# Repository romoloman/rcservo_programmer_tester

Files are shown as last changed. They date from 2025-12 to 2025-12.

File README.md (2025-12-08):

# RC Servo Programmer/Tester on Cheap Yellow Display*

A project to use a "Cheap Yellow Display" (based on ESP32) as Servo Programmer/Tester

## Project Description

This repository contains the code and instructions to turn a simple ESP32-based "Cheap Yellow Display" into a practical servo programmer and tester for RC Servo:
The tester work on any servo while at the moment the programmer works only on PTK Servos (other are planned to be supported). 
It allows you to change servo parameters as neutral angle, min/max PPM Values, Gain, Deadband and other.

The tester allow to place the servo at any position as well to perform continuos span between a minimum and maximun angle

It also allows to measure an incoming PPM signal from an RX displaying pulse width and frame frequency and also store minimum and maximum values of PPM pulses received

The goal is to provide a cheap, practical, on field usable, tool to program and test servos and check RX signals.

> [!WARNING]
> Place a 1k Ohm resistor in series on the signal cable coming from the RX if you want to use Pulse Meter functionalities

## Hardware Requirements

To build this project, you will need:
- A "Cheap Yellow Display" module (typically ESP32 with a 2.8" or 3.2" TFT display).
- A 470 Ohm resistor

If tou decide to print the box for the 2.8 Display you will need also:
- 1 - XT-30 Connector
- 1 - Male RC Servo connector
- 4 - M2.5 x 4 Screws

## Software Requirements

Arduino IDE
Esp32 Framework for arduino ide (tested up to version up to 3.3.4).
Necessary libraries for display management (install all of them from arduino library manager):
- TFT_eSPI (V2.5.43) - https://github.com/Bodmer/TFT_eSPI
- LVGL (9.4) - https://github.com/lvgl/lvgl
- XPT2046_Touchscreen (V1.4) - https://github.com/PaulStoffregen/XPT2046_Touchscreen

If you want to customize the interface you will also need EEZ Studio - https://github.com/eez-open/studio

Software includes copies of the following libraries adapted to work with ESP32 Framework V3:
- ServoESP32 library from alunit3 - https://github.com/alunit3/ServoESP32
- esp32-rmt-pwm-reader from rewegit - https://github.com/rewegit/esp32-rmt-pwm-reader  
 
## Installation and Setup

- Clone this repository to your computer.
- Open the project Arduino.
- Install the required libraries (check the specific instructions in the code or accompanying documentation).
- Select ESP32 Dev Module as target board
- Configure TFT_eSPI copying the user_setup.h from Config\(Display name) directory in your TFT_eSPI library folder, normally Documents\arduino\libraries\TFT_eSPI\
- Configure lvgl copying the lv_conf.h in the library folder, normally Documents\arduino\libraries\
- Compile to check that environment is OK
- Solder a 470 Ohm resistor between GPIO35 and GPIO22 (See Photo FOLDER)
- Connect signal wire from the servo connector and GPIO35
- Connect + and - from the xt30 connector to the CYD
- Connect the CYD to the USB port of your PC
- Upload the code to your Cheap Yellow Display.

## Usage

- Connect the xt30 connector to a 2S LiPo battery (or even to a 4S NiMh for standard servos).
- With the touch pen turn around to the display to autocalibrate touch (need to be redone at any firwmare update)
- Connect the servo to the servo connector Press "READ SERVO" to Read current configuration and "WRITE SERVO" to update it.

In servo tester page you can adjust value to your needs, by clicking on minimum pulse or maximum pulse values (the labels), the clicked value will be copied in the desidered servo position (useful to move immediately to either min/max position).

If servo tester is started the servo will move immediately to the selected position. By clicking on the position value, the value will be reset to the center (1500).

You can exit from programmer, servo tester and pulse meter pages by swiping the screen to the left.
    
## Contributing

Contributions are welcome! If you have ideas for improving the project, bug fixes, or new features, feel free to open an issue or submit a pull request.

## Screenshots 
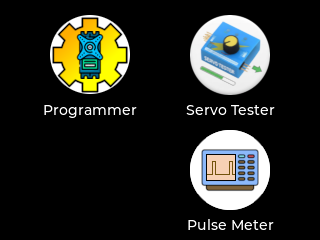
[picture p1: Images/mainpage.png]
Main page

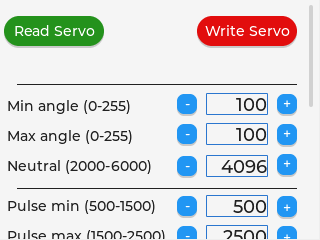
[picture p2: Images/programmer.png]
Servo programmer


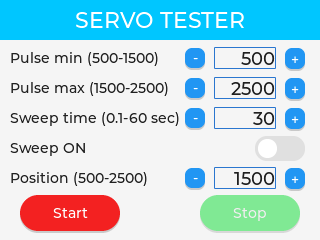
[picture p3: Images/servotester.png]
Servo tester

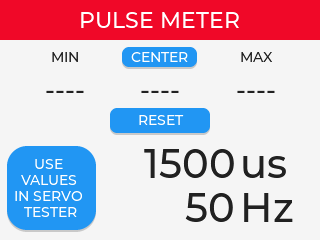
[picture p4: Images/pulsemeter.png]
Pulse meter


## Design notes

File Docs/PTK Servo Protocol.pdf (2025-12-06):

# Analysis of PTK Servo programming protocol

The protocol of PTK Servos like 8815, 8812 is not publicly documented, it was reverse engineered (accordingly to Directive (EU) 2009/24/EC ) by sniffing the servo signal wire with a logic analyzer. The tools used to perform this operation are:
- a cheap 8 channel login analyzer up to 24M samples per second
- sysrok pulseview logic analyzer software

### Servo Reading

Without any servo attached to the USB programmer 1
the software on the PC transmit a series of pulses and the stop. By analyzing minimum pulse width it was possible to determine the baud rate that is 115200.
By adding a UART Protocol decoder in the sysrok pulseview it was possible to see the 10 byte of the sequence: 175,250,0,10,56,0,0,0,0,66.
With the servo connected, 8 packets of 19 bytes are seen with a pause between each packet of about 50ms
N1 | 175 | 250 | 0 | 10 | 56 | 0 | 0 | 0 | 0 | 66 | 175 | 250 | 0 | 9 | 3 | 32 | 7 | 208 | 3
N2 | 175 | 250 | 0 | 10 | 61 | 0 | 0 | 0 | 0 | 71 | 175 | 250 | 0 | 9 | 0 | 29 | 0 | 12 | 50
N3 | 175 | 250 | 0 | 10 | 63 | 0 | 0 | 0 | 0 | 73 | 175 | 250 | 0 | 9 | 4 | 176 | 0 | 0 | 189
N4 | 175 | 250 | 0 | 10 | 80 | 0 | 0 | 0 | 0 | 90 | 175 | 250 | 0 | 9 | 7 | 208 | 39 | 16 | 23
N5 | 175 | 250 | 0 | 10 | 81 | 0 | 0 | 0 | 0 | 91 | 175 | 250 | 0 | 9 | 0 | 65 | 0 | 65 | 139
N6 | 175 | 250 | 0 | 10 | 82 | 0 | 0 | 0 | 0 | 92 | 175 | 250 | 0 | 9 | 16 | 0 | 0 | 0 | 25
N7 | 175 | 250 | 0 | 10 | 83 | 0 | 0 | 0 | 0 | 93 | 175 | 250 | 0 | 9 | 0 | 15 | 0 | 0 | 24
N8 | 175 | 250 | 0 | 10 | 84 | 0 | 0 | 0 | 0 | 94 | 175 | 250 | 0 | 9 | 0 | 1 | 0 | 0 | 10
As we can see the first part of N1 packet is exactly the same as without servo so the first 10 byte part should
be the inquiry and the second part should be the answer of the servo (the servo answers really very quickly)
Also we can see that there is a common pattern in the packets: apparently there is a common header of 175,250,0,10 for inquiries and 175,250,0,9 for answers.
It was rather simple to suppose that 175,250 (0xAF, 0XFA) is a header sequence and 0x00, 0x10 (or 0x00, 0x09) is the length of the packet in big endian format.
The fifth byte of the inquiry is a sort of command, then 4 zeros and reasonably there is a checksum. Understanding the checksum algorithm was rather tricky but the common pattern is that the sum of the bytes of the length plus the payload always matched with the checksum 0+10+56+0+0+0+0=66, the same is valid for the answer if the sum is made in an unsigned 8 bit number 0+9+3+32+7+208=259 → 259%256=3
To understand the meaning of the answer and by consequence understand the meaning of the inquiry command, servo parameters were changed one by one and the servo was reread after each change, the analysis brought to the following table:
N1 | 175 | 250 | 0 | 10 | 56 | 0 | 0 | 0 | 0 | 66 | 175 | 250 | 0 | 9 | 3 | 32 | 7 | 208 | 3
| Header | | Packet length | | Cmd | | | | | CK | Header | | Packet length | | Overload Power | | Overload time | | CK
N2 | 175 | 250 | 0 | 10 | 61 | 0 | 0 | 0 | 0 | 71 | 175 | 250 | 0 | 9 | 0 | 29 | 0 | 12 | 50
| Header | | Packet length | | Cmd | | | | | CK | Header | | Packet length | | Gain | | Dumping | | CK
N3 | 175 | 250 | 0 | 10 | 63 | 0 | 0 | 0 | 0 | 73 | 175 | 250 | 0 | 9 | 4 | 176 | 0 | 0 | 189
| Header | | Packet length | | Cmd | | | | | CK | Header | | Packet length | | Max Power | | | | CK
N4 | 175 | 250 | 0 | 10 | 80 | 0 | 0 | 0 | 0 | 90 | 175 | 250 | 0 | 9 | 7 | 208 | 39 | 16 | 23
| Header | | Packet length | | Cmd | | | | | CK | Header | | Packet length | | Min pulse width*4 | | Max pulse width*4 | | CK
N5 | 175 | 250 | 0 | 10 | 81 | 0 | 0 | 0 | 0 | 91 | 175 | 250 | 0 | 9 | 0 | 65 | 0 | 65 | 139
| Header | | Packet length | | Cmd | | | | | CK | Header | | Packet length | | Min Angle | | Max Angle | | CK
N6 | 175 | 250 | 0 | 10 | 82 | 0 | 0 | 0 | 0 | 92 | 175 | 250 | 0 | 9 | 16 | 0 | 0 | 0 | 25
| Header | | Packet length | | Cmd | | | | | CK | Header | | Packet length | | Neutral | | | | CK
N7 | 175 | 250 | 0 | 10 | 83 | 0 | 0 | 0 | 0 | 93 | 175 | 250 | 0 | 9 | 0 | 15 | 0 | 0 | 24
| Header | | Packet length | | Cmd | | | | | CK | Header | | Packet length | | Deadband | | | | CK
N8 | 175 | 250 | 0 | 10 | 84 | 0 | 0 | 0 | 0 | 94 | 175 | 250 | 0 | 9 | 0 | 1 | 0 | 0 | 10
| Header | | Packet length | | Cmd | | | | | CK | Header | | Packet length | | Inversion | | | | CK

The analysis confirmed that all values are sent/received MSB (Big Endian), It was not possible to determine Soft Start position as the 8812 and 8815 servos do not seem to support the function.

1 The USB programmer is a normal USB → Serial adapter with a 470 Ohm resistor connecting TX and RX to transform the adapter in a half duplex single wire serial

### Servo programming

An analysis with the logic analyzer was also made to the programming sequence by changing values one by one. To program the servo programming packet are sent with a logic of “fire and forget” the servo never answer to programming commands, the same sequence is also sent without servo attached.

N1 | 175 | 250 | 0 | 10 | 1 | 0 | 29 | 0 | 0 | 40
| Header | | Packet length | | Cmd | Gain | | | | CK
N2 | 175 | 250 | 0 | 10 | 5 | 0 | 12 | 0 | 0 | 27
| Header | | Packet length | | Cmd | Dumping | | | | CK
N3 | 175 | 250 | 0 | 10 | 18 | 3 | 32 | 7 | 208 | 22
| Header | | Packet length | | Cmd | Overload Power | | Overload Time | | CK
N4 | 175 | 250 | 0 | 10 | 24 | 4 | 176 | 0 | 0 | 214
| Header | | Packet length | | Cmd | Max Power | | | | CK
N5 | 175 | 250 | 0 | 10 | 64 | 0 | 0 | 0 | 65 | 139
| Header | | Packet length | | Cmd | | | Min Angle | | CK
N6 | 175 | 250 | 0 | 10 | 65 | 0 | 0 | 0 | 65 | 140
| Header | | Packet length | | Cmd | | | Max Angle | | CK
N7 | 175 | 250 | 0 | 10 | 66 | 0 | 0 | 16 | 0 | 92
| Header | | Packet length | | Cmd | | | Neutral | | CK
N8 | 175 | 250 | 0 | 10 | 67 | 0 | 0 | 0 | 15 | 92
| Header | | Packet length | | Cmd | | | Deadband | | CK
N9 | 175 | 250 | 0 | 10 | 68 | 0 | 0 | 0 | 1 | 79
| Header | | Packet length | | Cmd | | | Inversion | | CK
N10 | 175 | 250 | 0 | 10 | 69* | 0 | 0 | 0 | 0 | 79
| Header | | Packet length | | Cmd | unknown | | unknown | | CK
N11 | 175 | 250 | 0 | 10 | 72 | 7 | 208 | 39 | 16 | 96
| Header | | Packet length | | Cmd | Min pulse * 4 | | Max pulse * 4 | | CK
N12 | 175 | 250 | 0 | 10 | 70 | 0 | 0 | 0 | 1 | 81
| Header | | Packet length | | Cmd | | | Soft Start | | CK

* The command 69 (N10) is present but always write 0 0 0 0 as parameters the meaning is unknown.

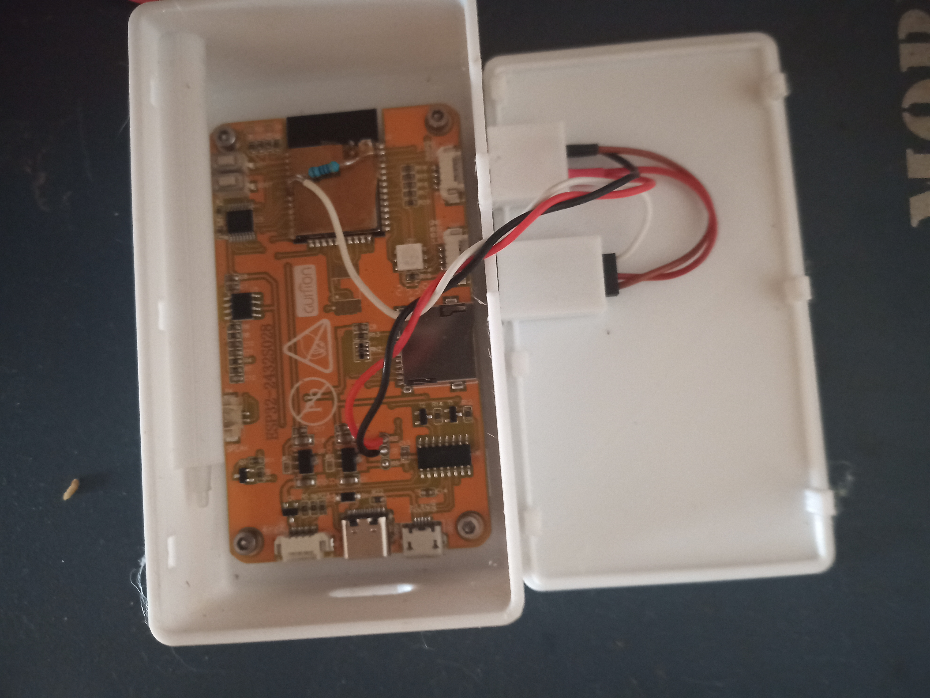
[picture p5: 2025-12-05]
Photo/Internal Overview.jpg

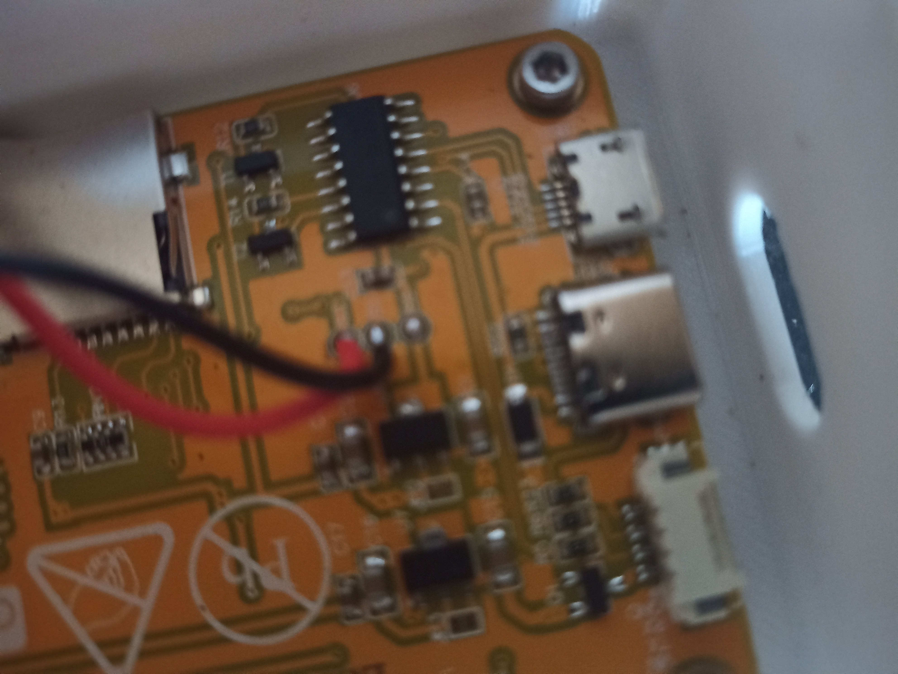
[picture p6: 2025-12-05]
Photo/ESP32 POWER Supply.jpg

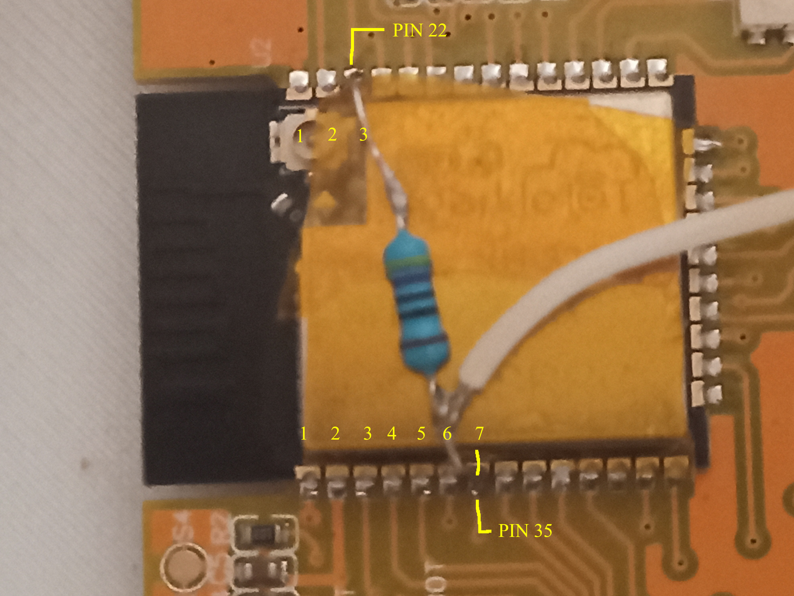
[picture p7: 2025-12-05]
Photo/ESP32 - 470Ohm - Servo Output.jpg

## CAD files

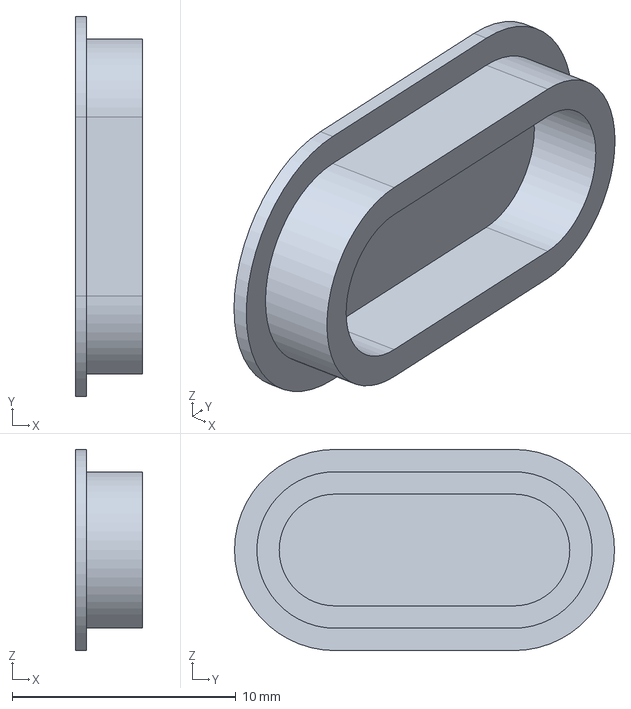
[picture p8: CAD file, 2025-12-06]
3D Models/ServoTester.FCStd
3.00 x 17.0 x 9.00 mm

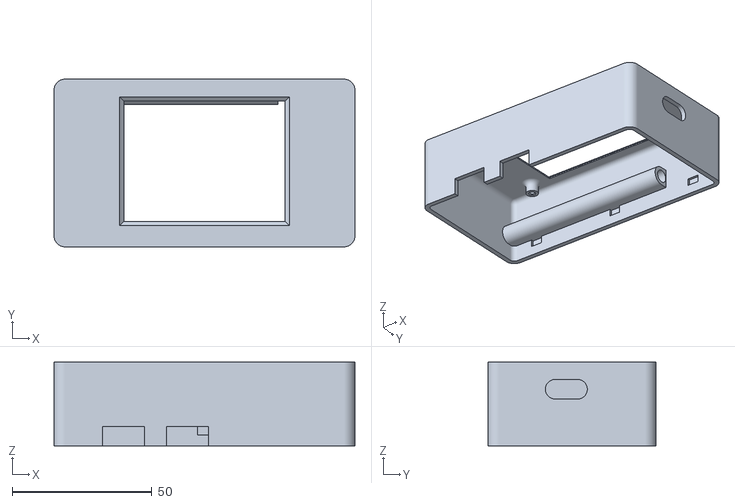
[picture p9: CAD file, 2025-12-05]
3D Models/Case-top.stl
107.6 x 60.0 x 30.0

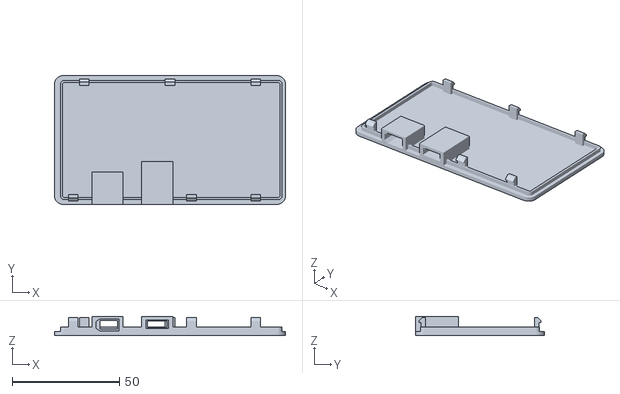
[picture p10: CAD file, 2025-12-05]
3D Models/Case-bottom.stl
107.6 x 60.0 x 9.00

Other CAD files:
3D Models/USB Tap.stl

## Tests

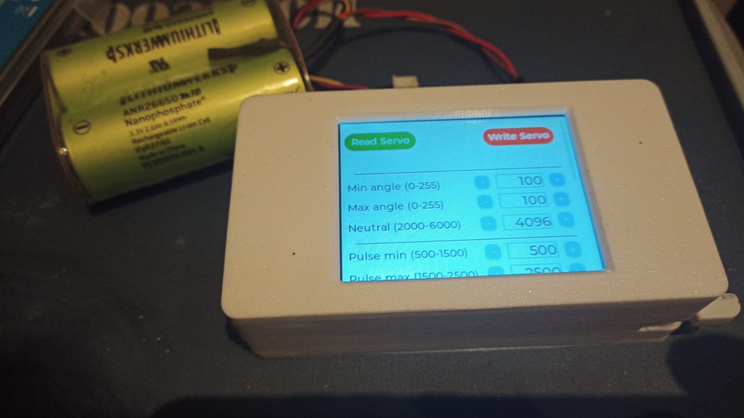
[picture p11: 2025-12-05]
Photo/ServoTester.jpg

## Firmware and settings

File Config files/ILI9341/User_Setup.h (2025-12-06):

/* 
  Rui Santos & Sara Santos - Random Nerd Tutorials

  Install the "TFT_eSPI" lbirary by Bodmer to interface with the TFT Display - https://github.com/Bodmer/TFT_eSPI
  *** IMPORTANT: User_Setup.h available on the internet will probably NOT work with the examples available at Random Nerd Tutorials ***
  *** YOU MUST USE THIS User_Setup.h FILE, CHECK FOR THE LATEST VERSION IN THE LINK BELOW IN ORDER TO USE THE EXAMPLES FROM RANDOM NERD TUTORIALS ***
  https://RandomNerdTutorials.com/cyd/
  https://RandomNerdTutorials.com/esp32-tft/
  FULL INSTRUCTIONS AVAILABLE ON HOW CONFIGURE THE LIBRARY: https://RandomNerdTutorials.com/cyd/ or https://RandomNerdTutorials.com/esp32-tft/
*/

//                            USER DEFINED SETTINGS
//   Set driver type, fonts to be loaded, pins used and SPI control method etc
//
//   See the User_Setup_Select.h file if you wish to be able to define multiple
//   setups and then easily select which setup file is used by the compiler.
//
//   If this file is edited correctly then all the library example sketches should
//   run without the need to make any more changes for a particular hardware setup!
//   Note that some sketches are designed for a particular TFT pixel width/height

// User defined information reported by "Read_User_Setup" test & diagnostics example
#define USER_SETUP_INFO "User_Setup"

// Define to disable all #warnings in library (can be put in User_Setup_Select.h)
//#define DISABLE_ALL_LIBRARY_WARNINGS

// ##################################################################################
//
// Section 1. Call up the right driver file and any options for it
//
// ##################################################################################

// Define STM32 to invoke optimised processor support (only for STM32)
//#define STM32

// Defining the STM32 board allows the library to optimise the performance
// for UNO compatible "MCUfriend" style shields
//#define NUCLEO_64_TFT
//#define NUCLEO_144_TFT

// STM32 8 bit parallel only:
// If STN32 Port A or B pins 0-7 are used for 8 bit parallel data bus bits 0-7
// then this will improve rendering performance by a factor of ~8x
//#define STM_PORTA_DATA_BUS
//#define STM_PORTB_DATA_BUS

// Tell the library to use parallel mode (otherwise SPI is assumed)
//#define TFT_PARALLEL_8_BIT
//#defined TFT_PARALLEL_16_BIT // **** 16 bit parallel ONLY for RP2040 processor ****

// Display type -  only define if RPi display
//#define RPI_DISPLAY_TYPE // 20MHz maximum SPI

// Only define one driver, the other ones must be commented out
//#define ILI9341_DRIVER       // Generic driver for common displays

#define ILI9341_2_DRIVER     // Alternative ILI9341 driver, see https://github.com/Bodmer/TFT_eSPI/issues/1172
//#define ST7735_DRIVER      // Define additional parameters below for this display
//#define ILI9163_DRIVER     // Define additional parameters below for this display
//#define S6D02A1_DRIVER
//#define RPI_ILI9486_DRIVER // 20MHz maximum SPI
//#define HX8357D_DRIVER
//#define ILI9481_DRIVER
//#define ILI9486_DRIVER
//#define ILI9488_DRIVER     // WARNING: Do not connect ILI9488 display SDO to MISO if other devices share the SPI bus (TFT SDO does NOT tristate when CS is high)
//#define ST7789_DRIVER      // Full configuration option, define additional parameters below for this display
//#define ST7789_2_DRIVER    // Minimal configuration option, define additional parameters below for this display
//#define R61581_DRIVER
//#define RM68140_DRIVER
//#define ST7796_DRIVER
//#define SSD1351_DRIVER
//#define SSD1963_480_DRIVER
//#define SSD1963_800_DRIVER
//#define SSD1963_800ALT_DRIVER
//#define ILI9225_DRIVER
//#define GC9A01_DRIVER

// Some displays support SPI reads via the MISO pin, other displays have a single
// bi-directional SDA pin and the library will try to read this via the MOSI line.
// To use the SDA line for reading data from the TFT uncomment the following line:

// #define TFT_SDA_READ      // This option is for ESP32 ONLY, tested with ST7789 and GC9A01 display only

// For ST7735, ST7789 and ILI9341 ONLY, define the colour order IF the blue and red are swapped on your display
// Try ONE option at a time to find the correct colour order for your display

//  #define TFT_RGB_ORDER TFT_RGB  // Colour order Red-Green-Blue
#define TFT_RGB_ORDER TFT_BGR  // Colour order Blue-Green-Red

// For M5Stack ESP32 module with integrated ILI9341 display ONLY, remove // in line below

// #define M5STACK

// For ST7789, ST7735, ILI9163 and GC9A01 ONLY, define the pixel width and height in portrait orientation
// #define TFT_WIDTH  80
// #define TFT_WIDTH  128
// #define TFT_WIDTH  172 // ST7789 172 x 320
#define TFT_WIDTH  240 // ST7789 240 x 240 and 240 x 320
// #define TFT_HEIGHT 160
// #define TFT_HEIGHT 128
// #define TFT_HEIGHT 240 // ST7789 240 x 240
#define TFT_HEIGHT 320 // ST7789 240 x 320
// #define TFT_HEIGHT 240 // GC9A01 240 x 240

// For ST7735 ONLY, define the type of display, originally this was based on the
// colour of the tab on the screen protector film but this is not always true, so try
// out the different options below if the screen does not display graphics correctly,
// e.g. colours wrong, mirror images, or stray pixels at the edges.
// Comment out ALL BUT ONE of these options for a ST7735 display driver, save this
// this User_Setup file, then rebuild and upload the sketch to the board again:

// #define ST7735_INITB
// #define ST7735_GREENTAB
// #define ST7735_GREENTAB2
// #define ST7735_GREENTAB3
// #define ST7735_GREENTAB128    // For 128 x 128 display
// #define ST7735_GREENTAB160x80 // For 160 x 80 display (BGR, inverted, 26 offset)
// #define ST7735_ROBOTLCD       // For some RobotLCD arduino shields (128x160, BGR, https://docs.arduino.cc/retired/getting-started-guides/TFT)
// #define ST7735_REDTAB
// #define ST7735_BLACKTAB
// #define ST7735_REDTAB160x80   // For 160 x 80 display with 24 pixel offset

// If colours are inverted (white shows as black) then uncomment one of the next
// 2 lines try both options, one of the options should correct the inversion.

// #define TFT_INVERSION_ON
#define TFT_INVERSION_OFF


// ##################################################################################
//
// Section 2. Define the pins that are used to interface with the display here
//
// ##################################################################################

// If a backlight control signal is available then define the TFT_BL pin in Section 2
// below. The backlight will be turned ON when tft.begin() is called, but the library
// needs to know if the LEDs are ON with the pin HIGH or LOW. If the LEDs are to be
// driven with a PWM signal or turned OFF/ON then this must be handled by the user
// sketch. e.g. with digitalWrite(TFT_BL, LOW);

#define TFT_BL   21            // LED back-light control pin
#define TFT_BACKLIGHT_ON HIGH  // Level to turn ON back-light (HIGH or LOW)
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

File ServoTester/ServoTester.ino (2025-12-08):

#include <Arduino.h>
#include <lvgl.h>
#include <TFT_eSPI.h>
#include "ui.h"
#include <EEPROM.h>
#include "esp32-rmt-pwm-reader.h"
#include "Servo.h"
Servo myservo;  // create servo object to control a servo
#define LEDR 4
#define LEDB 16
#define LEDG 17

#define RxSerial Serial1
#define TxSerial Serial2
#define TXSERIAL_PIN 22  // pin for trasmitting command to servo and PWM signal
#define IGNRXSER_PIN 27  // unused pin for serial rx
#define READ_PIN 35      // pin used to read answers from SERVO

const uint8_t channelPins[]={READ_PIN};

// Set the following to true for serial debugging
#define DEBUG false
#define DEBUGREADCHARS false
char buffer[30];
uint8_t redrawScreen = 0;
uint8_t readServo = 0;
uint8_t writeServo = 0;
uint8_t ServoTestOn = 0;
uint8_t ServoAttached = 0;
uint8_t MeterOn = 0;
uint8_t MeterAttached = 0;
uint8_t CalUpdated = 0;
unsigned long lasteepromwrite;
float ServoPosition = 1500;
float ServoIncrement = 0;
uint8_t SweepStarted = 0;
int16_t SweepDirection = 1;

#include <TFT_eSPI.h>

#include <XPT2046_Touchscreen.h>
// A library for interfacing with the touch screen
//
// Can be installed from the library manager (Search for "XPT2046")
//https://github.com/PaulStoffregen/XPT2046_Touchscreen
// ----------------------------
// Touch Screen pins
// ----------------------------

// The CYD touch uses some non default
// SPI pins

#define XPT2046_IRQ 36
#define XPT2046_MOSI 32
#define XPT2046_MISO 39
#define XPT2046_CLK 25
#define XPT2046_CS 33
SPIClass touchscreenSpi = SPIClass(VSPI);
XPT2046_Touchscreen touchscreen(XPT2046_CS, XPT2046_IRQ);
uint16_t touchScreenMinimumX = 400, touchScreenMaximumX = 3000, touchScreenMinimumY = 500, touchScreenMaximumY = 3000;

extern objects_t objects;
/*Set to your screen resolution*/
#define TFT_HOR_RES 240
#define TFT_VER_RES 320

/*LVGL draw into this buffer, 1/10 screen size usually works well. The size is in bytes*/
#define DRAW_BUF_SIZE (TFT_HOR_RES * TFT_VER_RES / 10 * (LV_COLOR_DEPTH / 8))


#if LV_USE_LOG != 0
void my_print(lv_log_level_t level, const char *buf) {
  LV_UNUSED(level);
#if DEBUG
  Serial.println(buf);
  Serial.flush();
#endif
}
#endif

/* LVGL calls it when a rendered image needs to copied to the display*/
void my_disp_flush(lv_display_t *disp, const lv_area_t *area, uint8_t *px_map) {
  /*Call it to tell LVGL you are ready*/
  lv_disp_flush_ready(disp);
}

/*Read the touchpad*/
void my_touchpad_read(lv_indev_t *indev, lv_indev_data_t *data) {
  if (touchscreen.touched()) {
    TS_Point p = touchscreen.getPoint();
    //Some very basic auto calibration so it doesn't go out of range
    if (p.x < touchScreenMinimumX) {
      touchScreenMinimumX = p.x;
      CalUpdated = 1;
#if DEBUG
      Serial.printf("Recalibrating touchScreenMinimumX %d\n", touchScreenMinimumX);
#endif
    }
    if (p.x > touchScreenMaximumX) {
      touchScreenMaximumX = p.x;
      CalUpdated = 1;
#if DEBUG
      Serial.printf("Recalibrating touchScreenMaximumX %d\n", touchScreenMaximumX);
#endif
    }
    if (p.y < touchScreenMinimumY) {
      touchScreenMinimumY = p.y;
      CalUpdated = 1;
#if DEBUG
      Serial.printf("Recalibrating touchScreenMinimumY %d\n", touchScreenMinimumY);
#endif
    }
    if (p.y > touchScreenMaximumY) {
      touchScreenMaximumY = p.y;
      CalUpdated = 1;
#if DEBUG
      Serial.printf("Recalibrating touchScreenMaximumY %d\n", touchScreenMaximumY);
#endif
    }
    //Map this to the pixel position
    data->point.x = map(p.x, touchScreenMinimumX, touchScreenMaximumX, 0, TFT_HOR_RES - 1); /* Touchscreen X calibration */
    data->point.y = map(p.y, touchScreenMinimumY, touchScreenMaximumY, 0, TFT_VER_RES - 1); /* Touchscreen Y calibration */
#if DEBUG
    Serial.printf("X: %d, Y: %d\n", data->point.x, data->point.y);
#endif
    data->state = LV_INDEV_STATE_PRESSED;
  } else {
    data->state = LV_INDEV_STATE_RELEASED;
  }
}

lv_indev_t *indev;      //Touchscreen input device
uint8_t *draw_buf;      //draw_buf is allocated on heap otherwise the static area is too big on ESP32 at compile
uint32_t lastTick = 0;  //Used to track the tick timer
uint32_t currentTime, displayTime;

struct servostruct {
  uint8_t min_angle;
  uint8_t max_angle;
  uint16_t neutral_angle;
  uint16_t min_pulse;
  uint16_t max_pulse;
  uint8_t deadband;
  uint8_t gain;
  uint8_t dumping;
  uint16_t max_power;
  uint16_t oltime;
  uint16_t olpower;
  uint8_t inversion;
  uint8_t softstart;
};
servostruct servo;
servostruct servoquery;

struct stteststruct {
  uint16_t min_pulse;
  uint16_t max_pulse;
  uint16_t sweeptime;
  uint8_t sweepon;
  uint16_t position;
};
stteststruct sttest;

struct pulsemeterstruct {
  uint16_t min_pulse;
  uint16_t max_pulse;
  uint16_t center_pulse;
  unsigned long lastinput;
  unsigned long pulseInValue;
  unsigned long frameInValue;
};
volatile pulsemeterstruct pulseMeter;

void loadservodefault() {
  servo.min_angle = 100;
  servo.max_angle = 100;
  servo.neutral_angle = 4096;
  servo.min_pulse = 500;
  servo.max_pulse = 2500;
  servo.deadband = 15;
  servo.gain = 29;
  servo.dumping = 12;
  servo.max_power = 1200;
  servo.oltime = 2000;
  servo.olpower = 1200;
  servo.inversion = 0;
  servo.softstart = 0;
  sttest.min_pulse = 500;
  sttest.max_pulse = 2500;
  sttest.sweeptime = 5;
  sttest.sweepon = 0;
  sttest.position = 1500;
}
uint8_t basecommand[] = { 175, 250, 0, 10, 0, 0, 0, 0, 0, 0 };
uint8_t readcommands[] = { 56, 61, 63, 80, 81, 82, 83, 84 };
uint8_t writecommands[] = { 1, 5, 18, 24, 64, 65, 66, 67, 68, 69, 72, 70 };

void ServoWrite(uint8_t command, uint16_t payloadh, uint16_t payloadl) {
  uint8_t checksum = 0;
  basecommand[4] = command;
  basecommand[5] = (payloadh >> 8);
  basecommand[6] = (payloadh % 256);
  basecommand[7] = (payloadl >> 8);
  basecommand[8] = (payloadl % 256);
  for (int i = 2; i < 9; i++) {
    checksum += basecommand[i];
  }
  basecommand[9] = checksum;
  TxSerial.write(basecommand, 10);
  TxSerial.flush();
}

bool ReadAnswer(uint8_t command) {
  uint8_t ch;
  uint8_t checksum = 0;
  int8_t readchars = 0;
  char buffer[30];
  while (RxSerial.available() && readchars < 30) {
    ch = (byte)RxSerial.read();
    buffer[readchars] = ch;
#if DEBUGREADCHARS
    Serial.printf("%d ,", ch);
#endif
    readchars++;
  }
  Serial.println();
  if (readchars != 19 || buffer[4] != command) {
#if DEBUG
    Serial.printf("Readdchars %d \n\r", readchars);
    Serial.printf("Buffer 4 %d \n\r", buffer[4]);
#endif
    return false;
  }
  for (int i = 12; i < 18; i++) {
    checksum += buffer[i];
  }
  if (checksum != buffer[18]) {
#if DEBUG
    Serial.println("Checksum failed");
#endif
    return false;
  }
  switch (command) {
    case 56:
      servoquery.olpower = buffer[14];
      servoquery.olpower *= 256;
      servoquery.olpower += buffer[15];
      servoquery.oltime = buffer[16];
      servoquery.oltime *= 256;
      servoquery.oltime += buffer[17];
#if DEBUG
      Serial.print("OLPOWER:");
      Serial.println(servoquery.olpower);
      Serial.print("OLTIME:");
      Serial.println(servoquery.oltime);
#endif
      break;
    case 61:
      servoquery.gain = buffer[14];
      servoquery.gain *= 256;
      servoquery.gain += buffer[15];
      servoquery.dumping = buffer[16];
      servoquery.dumping *= 256;
      servoquery.dumping += buffer[17];
#if DEBUG
      Serial.print("GAIN:");
      Serial.println(servoquery.gain);
      Serial.print("DUMPING:");
      Serial.println(servoquery.dumping);
#endif
      break;
    case 63:
      servoquery.max_power = buffer[14];
      servoquery.max_power *= 256;
      servoquery.max_power += buffer[15];
#if DEBUG
      Serial.print("MAXPOWER:");
      Serial.println(servoquery.max_power);
#endif
      break;
    case 80:
      servoquery.min_pulse = buffer[14];
      servoquery.min_pulse *= 256;
      servoquery.min_pulse += buffer[15];
      servoquery.min_pulse /= 4;
      servoquery.max_pulse = buffer[16];
      servoquery.max_pulse *= 256;
      servoquery.max_pulse += buffer[17];
      servoquery.max_pulse /= 4;
#if DEBUG
      Serial.print("MIN_PULSE:");
      Serial.println(servoquery.min_pulse);
      Serial.print("MAX_PULSE:");
      Serial.println(servoquery.max_pulse);
#endif
      break;
    case 81:
      servoquery.min_angle = buffer[15];
      servoquery.max_angle = buffer[17];
#if DEBUG
      Serial.print("MIN_ANGLE:");
      Serial.println(servoquery.min_angle);
      Serial.print("MAX_ANGLE:");
      Serial.println(servoquery.max_angle);
#endif
      break;
    case 82:
      servoquery.neutral_angle = buffer[14];
      servoquery.neutral_angle *= 256;
      servoquery.neutral_angle += buffer[15];
#if DEBUG
      Serial.print("NEUTRAL_ANGLE:");
      Serial.println(servoquery.neutral_angle);
#endif
      break;
    case 83:
      servoquery.deadband = buffer[15];
#if DEBUG
      Serial.print("DEADBAND:");
      Serial.println(servoquery.deadband);
#endif
      break;
    case 84:
      servoquery.inversion = buffer[15];
      servoquery.softstart = buffer[17];
#if DEBUG
      Serial.print("INVERSION:");
      Serial.println(servoquery.inversion);
      Serial.print("SOFTSTART:");
      Serial.println(servoquery.softstart);
#endif
      break;
    default:
      return false;
      break;
  }
  return true;
}

bool ServoRead() {
  uint8_t command;
  uint8_t index = 0;
  while (index < 8) {
    ServoWrite(readcommands[index], 0, 0);
    delay(5);
    if (!ReadAnswer(readcommands[index])) {
#if DEBUG
      Serial.println("Read Failed");
#endif
      break;
    } else {
#if DEBUG
      Serial.println("Read Success");
#endif
      index++;
    }
    delay(50);
  }
  if (index == 8) {
    servo = servoquery;
    return true;
  } else {
    return false;
  }
}

void UpdateServo() {
  uint8_t command;
  uint8_t index = 0;
  uint16_t payloadh = 0;
  uint16_t payloadl = 0;
  while (index < 12) {
    payloadh = 0;
    payloadl = 0;
    command = writecommands[index];
    switch (command) {
      case 1:
        payloadh = servo.gain;
        break;
      case 5:
        payloadh = servo.dumping;
        break;
      case 18:
        payloadh = servo.oltime;
        payloadl = servo.olpower;
        break;
      case 24:
        payloadh = servo.max_power;
        break;
      case 64:
        payloadl = servo.min_angle;
        break;
      case 65:
        payloadl = servo.max_angle;
        break;
      case 66:
        payloadl = servo.neutral_angle;
        break;
      case 67:
        payloadl = servo.deadband;
        break;
      case 68:
        payloadl = servo.inversion;
        break;
      case 69:
        break;
      case 72:
        payloadh = servo.min_pulse * 4;
        payloadl = servo.max_pulse * 4;
        break;
      case 70:
        payloadl = servo.softstart;
        break;
    }
    ServoWrite(command, payloadh, payloadl);
    delay(50);
    index++;
  }
}

void setup() {
  // Initialization function
  // Some basic info on the Serial console
  pinMode(LEDR, OUTPUT);
  pinMode(LEDG, OUTPUT);
  pinMode(LEDB, OUTPUT);
  digitalWrite(LEDR, HIGH);
  digitalWrite(LEDG, HIGH);
  digitalWrite(LEDB, HIGH);

#if DEBUG
  delay(2000);
  String LVGL_Arduino = "LVGL demo ";
  LVGL_Arduino += String('V') + lv_version_major() + "." + lv_version_minor() + "." + lv_version_patch();
  Serial.begin(115200);
  Serial.println(LVGL_Arduino);
#endif
  if (!EEPROM.begin(100)) {
#if DEBUG
    Serial.println("Failed to initialize EEPROM");
    Serial.println("Restarting...");
#endif
    delay(1000);
    ESP.restart();
  }
  int address = 0;
  int value;
  value = EEPROM.readUInt(address);
  if (value > 100) {
    touchScreenMinimumX = value;
  }
  address += sizeof(unsigned int);
  value = EEPROM.readUInt(address);
  if (value > 100) {
    touchScreenMaximumX = value;
  }
  address += sizeof(unsigned int);
  value = EEPROM.readUInt(address);
  if (value > 100) {
    touchScreenMinimumY = value;
  }
  address += sizeof(unsigned int);
  value = EEPROM.readUInt(address);
  if (value > 100) {
    touchScreenMaximumY = value;
  }

  // Initialise the touchscreen
  touchscreenSpi.begin(XPT2046_CLK, XPT2046_MISO, XPT2046_MOSI, XPT2046_CS); /* Start second SPI bus for touchscreen */
  touchscreen.begin(touchscreenSpi);                                         /* Touchscreen init */
  touchscreen.setRotation(2);                                                /* Inverted landscape orientation to match screen */

  // Initialise LVGL GUI
  lv_init();

  // Setup LVGL display and input devices
  draw_buf = new uint8_t[DRAW_BUF_SIZE];
  lv_display_t *disp;
  disp = lv_tft_espi_create(TFT_HOR_RES, TFT_VER_RES, draw_buf, DRAW_BUF_SIZE);
  lv_display_set_rotation(disp, LV_DISPLAY_ROTATION_270);
  // Initialize the XPT2046 input device driver
  indev = lv_indev_create();
  lv_indev_set_type(indev, LV_INDEV_TYPE_POINTER);
  lv_indev_set_read_cb(indev, my_touchpad_read);

  // Integrate EEZ Studio GUI (initialize UI elements based on definition)
  ui_init();
  digitalWrite(21, HIGH);  // Turn on display
  pinMode(READ_PIN, INPUT);
  pinMode(TXSERIAL_PIN, INPUT_PULLUP);

  /*
  TxSerial.begin(115200, EspSoftwareSerial::SWSERIAL_8N1, READ_PIN, READ_PIN , false, 256);
	// high speed half duplex, turn off interrupts during tx
	TxSerial.enableIntTx(false);
*/
  loadservodefault();
  redrawScreen = 1;
}

unsigned long now;
unsigned long lastsweep;
unsigned long nowmicros;
unsigned long lastservo;
unsigned long lastinputredraw;

void loop() {
  // Main program loop
  now = millis();
  nowmicros = micros();
  if ((CalUpdated == 1) && (now - lasteepromwrite) > 30000ull) {
#if DEBUG
    Serial.println("Save settings");
#endif
    int address = 0;
    EEPROM.writeUInt(address, touchScreenMinimumX);  // -2^31
    address += sizeof(unsigned int);
    EEPROM.writeUInt(address, touchScreenMaximumX);  // -2^31
    address += sizeof(unsigned int);
    EEPROM.writeUInt(address, touchScreenMinimumY);  // -2^31
    address += sizeof(unsigned int);
    EEPROM.writeUInt(address, touchScreenMaximumY);  // -2^31
    EEPROM.commit();
    lasteepromwrite = now;
    CalUpdated = 0;
  }

  if (readServo == 1 || writeServo == 1) {
    ServoTestOn = 0;
    MeterOn = 0;
  }

  if (MeterOn == 1) {
    ServoTestOn = 0;
  }

  if (ServoTestOn == 1) {
    if (ServoAttached == 0) {
      myservo.attach(TXSERIAL_PIN, Servo::CHANNEL_NOT_ATTACHED, 10, 170, 500, 2500);
      ServoAttached = 1;
    }
    if (sttest.sweepon == 0) {
      myservo.writeMicroseconds(sttest.position);
      delay(15);
    } else {
      if (SweepStarted == 0) {
#if DEBUG
        Serial.println("Doing Servo Sweep");
#endif
        ServoPosition = (sttest.min_pulse);
        myservo.writeMicroseconds((uint16_t)round(ServoPosition));
        delay(200);
        SweepStarted = 1;
        SweepDirection = 1;
        lastsweep = nowmicros;
      } else {
        if ((nowmicros - lastsweep) > 19900) {
          lastsweep = nowmicros;
          ServoIncrement = ((float)(sttest.max_pulse - sttest.min_pulse)) / (5 * sttest.sweeptime);
          if (SweepDirection == 1) {
            ServoPosition += ServoIncrement;
            if (ServoPosition > ((float)sttest.max_pulse)) {
              ServoPosition = sttest.max_pulse;
              SweepDirection = -1;
            }
          } else {
            ServoPosition -= ServoIncrement;
            if (ServoPosition < ((float)sttest.min_pulse)) {
              ServoPosition = sttest.min_pulse;
              SweepDirection = 1;
            }
          }
          myservo.writeMicroseconds((uint16_t)ServoPosition);
        }
      }
    }
  } else if (ServoAttached == 1) {
    myservo.detach();
    pinMode(TXSERIAL_PIN, INPUT_PULLUP);
    ServoAttached = 0;
    SweepStarted = 0;
    SweepDirection = 1;
    lv_obj_remove_state(objects.ststartbt, LV_STATE_DISABLED);
    lv_obj_set_state(objects.ststopbt, LV_STATE_DISABLED, LV_ANIM_ON);
    delay(100);
  }
  if (MeterOn == 1) {
    if (MeterAttached==0) {
      pwm_reader_init(channelPins, 1);
      pwm_set_failsafe(0, false);
      pwm_set_auto_zero(0, true);     // set channel to auto zero
      pwm_set_auto_min_max(0, true);  // set channel to auto min/max calibration
      pwm_reader_begin();      
      pulseMeter.min_pulse=2500;
      pulseMeter.max_pulse=0;
      pulseMeter.center_pulse=0;      
      MeterAttached=1;
    }
    if (pwm_get_state(0)==PwmState::STABLE) {
      pulseMeter.pulseInValue=pwm_get_rawPwm(0);
      if (pulseMeter.pulseInValue==-1) {
        pulseMeter.pulseInValue=0;
      }
      pulseMeter.frameInValue=pwm_get_frequency(0);
      pulseMeter.lastinput=now;
    }
    if ((now - pulseMeter.lastinput) > 200) {
      pulseMeter.pulseInValue = 0;
      pulseMeter.frameInValue = 0;
    } 
    if (pulseMeter.pulseInValue!=0) {
      if (pulseMeter.pulseInValue>pulseMeter.max_pulse) {
        pulseMeter.max_pulse=pulseMeter.pulseInValue;
        sprintf(buffer, "%d", pulseMeter.pulseInValue);
        lv_label_set_text(objects.metermaxvaluelbl, buffer);
      }
      if (pulseMeter.pulseInValue<pulseMeter.min_pulse) {
        pulseMeter.min_pulse=pulseMeter.pulseInValue;
        sprintf(buffer, "%d", pulseMeter.pulseInValue);
        lv_label_set_text(objects.meterminvaluelbl, buffer);
      }
    }
    if ((now - lastinputredraw) > 100ull) {
      if (pulseMeter.pulseInValue != 0) {
        sprintf(buffer, "%d", pulseMeter.pulseInValue);
        lv_label_set_text(objects.pulsevaluelbl, buffer);
      } else {
        lv_label_set_text(objects.pulsevaluelbl, "----");
      }
      if (pulseMeter.frameInValue != 0) {
        sprintf(buffer, "%d", pulseMeter.frameInValue);
        lv_label_set_text(objects.frequencyvaluelbl, buffer);
      } else {
        lv_label_set_text(objects.frequencyvaluelbl, "---");
      }
      lastinputredraw = now;
    }
  } else {
    if (MeterAttached==1) {
      pwm_cleanup();
      MeterAttached=0;
    }
  }
  if (readServo == 1) {
    RxSerial.begin(115200, SERIAL_8N1, READ_PIN, -1);
    RxSerial.setTimeout(0);
    TxSerial.begin(115200, SERIAL_8N1, IGNRXSER_PIN, TXSERIAL_PIN);
    TxSerial.setTimeout(0);
    while (RxSerial.available()) {
      uint8_t receivedChar = RxSerial.read();
    }
    if (ServoRead()) {
      lv_label_set_text(objects.msglbl, "Read Success");
    } else {
      lv_label_set_text(objects.msglbl, "Read Failed");
    }
    lastservo = now;
    redrawScreen = 1;
    readServo = 0;
    delay(100);
    TxSerial.end();
    pinMode(TXSERIAL_PIN, INPUT_PULLUP);
    RxSerial.end();
    pinMode(READ_PIN, INPUT);
  }
  if (writeServo == 1) {
    RxSerial.begin(115200, SERIAL_8N1, READ_PIN, -1);
    RxSerial.setTimeout(0);
    TxSerial.begin(115200, SERIAL_8N1, IGNRXSER_PIN, TXSERIAL_PIN);
    TxSerial.setTimeout(0);
    while (RxSerial.available()) {
      uint8_t receivedChar = RxSerial.read();
    }
    UpdateServo();
    lv_label_set_text(objects.msglbl, "Update done.");
    lastservo = now;
    redrawScreen = 1;
    writeServo = 0;
    delay(100);
    TxSerial.end();
    pinMode(TXSERIAL_PIN, INPUT_PULLUP);
    RxSerial.end();
    pinMode(READ_PIN, INPUT);
  }

  if (now - lastservo > 5000ull) {
    lv_obj_remove_state(objects.readservo, LV_STATE_DISABLED);
    lv_obj_remove_state(objects.writeservo, LV_STATE_DISABLED);
    lv_label_set_text(objects.msglbl, "");
    lastservo = now;
  }

  if (redrawScreen == 1) {
    sprintf(buffer, "%d", servo.min_angle);
    lv_label_set_text(objects.minanglelbl, buffer);
    sprintf(buffer, "%d", servo.max_angle);
    lv_label_set_text(objects.maxanglelbl, buffer);
    sprintf(buffer, "%d", servo.neutral_angle);
    lv_label_set_text(objects.neutrallbl, buffer);
    sprintf(buffer, "%d", servo.deadband);
    lv_label_set_text(objects.deadbandlbl, buffer);
    sprintf(buffer, "%d", servo.dumping);
    lv_label_set_text(objects.dumpinglbl, buffer);
    sprintf(buffer, "%d", servo.gain);
    lv_label_set_text(objects.gainlbl, buffer);
    sprintf(buffer, "%d", servo.min_pulse);
    lv_label_set_text(objects.pulseminlbl, buffer);
    sprintf(buffer, "%d", servo.max_pulse);
    lv_label_set_text(objects.pulsemaxlbl, buffer);
    sprintf(buffer, "%d", servo.max_power);
    lv_label_set_text(objects.powerlbl, buffer);
    sprintf(buffer, "%d", servo.oltime);
    lv_label_set_text(objects.oltimelbl, buffer);
    sprintf(buffer, "%d", servo.olpower);
    lv_label_set_text(objects.ololpowerlbl, buffer);
    if (servo.inversion == 1) {
      lv_obj_set_state(objects.inversionsw, LV_STATE_CHECKED, LV_ANIM_ON);
    } else {
      lv_obj_remove_state(objects.inversionsw, LV_STATE_CHECKED);
    }
    if (servo.softstart == 1) {
      lv_obj_set_state(objects.softstartsw, LV_STATE_CHECKED, LV_ANIM_ON);
    } else {
      lv_obj_remove_state(objects.softstartsw, LV_STATE_CHECKED);
    }
    sprintf(buffer, "%d", sttest.min_pulse);
    lv_label_set_text(objects.stpulseminlbl, buffer);
    sprintf(buffer, "%d", sttest.max_pulse);
    lv_label_set_text(objects.stpulsemaxlbl, buffer);
    sprintf(buffer, "%0.1f", ((float)sttest.sweeptime) / 10);
    lv_label_set_text(objects.stsweeplbl, buffer);
    if (sttest.sweepon == 1) {
      lv_obj_set_state(objects.stsweepsw, LV_STATE_CHECKED, LV_ANIM_ON);
    } else {
      lv_obj_remove_state(objects.stsweepsw, LV_STATE_CHECKED);
    }
    sprintf(buffer, "%d", sttest.position);
    lv_label_set_text(objects.stcenterlbl, buffer);
    redrawScreen = 0;
  }
  lv_tick_inc(now - lastTick);  // Update the LVGL tick timer
  lastTick = now;
  lv_timer_handler();  // Update the UI (LVGL)
}

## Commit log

2025-12-05 Initial commit
    Initial commit of the project
    [provaservi-scatola.stl, provaservi-tappo.stl]
2025-12-05 Add missing 3d model part
    [USB Tap.stl]
2025-12-06 Update PTK Servo Protocol.pdf
2025-12-06 Rename 3D Models
    [Case-bottom.stl, Case-top.stl]
2025-12-06 Set correct SPI frequency for ILI9341
    [User_Setup.h]
2025-12-06 Interface update
    Update user interface, removed dependancy from ESP32Servo library
2025-12-08 User rmt to read pwm instead of interrupts
2025-12-08 esp32-rmt-pwm-reader updates
    Adapted esp32-rmt-pwm-reader library to new rmt_rx driver for idf > 5.0
